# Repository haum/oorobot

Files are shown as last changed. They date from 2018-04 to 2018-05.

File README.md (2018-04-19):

logo_s

# OoRoBoT : Un robot éducatif à construire soi-même

L'idée est de créer un robot éducatif destiné aux enfants de maternelle et élémentaire sur le principe de [la BeeBot](http://www.robotsenclasse.ch/robots-en-classe/beebot), tout en suivant les contraintes suivantes :
- Mettre le projet en OpenSource : page github avec le code, la liste de matériel et les plans nécessaires
- Utiliser du matériel électronique standard (Arduino) et peu onéreux
- Éviter les opérations "complexes" (soudure, usinage)

Au fil des évolutions du projet, l'OoRoBoT apporte tout un lot de fonctionnalités complémentaires :
- Présence d'un écran LCD de 2 lignes de 16 caractères permettant à l'enfant de visualiser le programme qu'il écrit. Cet écran associé au clavier permet aussi de régler le robot très précisement
- Ajout d'une interface Bluetooth permettant de piloter le robot à distance et ainsi permettre de lui donner des ordres complexes (boucles, tracé d'arc de cercle ...)
- Ajout d'un servomoteur afin de baisser/lever un crayon

Actuellement le robot peut être utilisé de deux façons différentes (comme indiqué dans sur [ce poster](doc/com/oorobot_poster-LIGHT.pdf)) :
- Pour les enfants de 4 à 7 ans : programmer des parcours sur des plateaux (voir les plateaux disponibles dans le [répertoire /doc/exercices](/doc/exercices))
- Pour les enfants de 7 à 12 ans : réaliser des tracés avec un langage de programmation par blocs. Vous pouvez vous entrainer à faire des tracés sur [cette page Web](https://orange-opensource.github.io/oorobot/blocks/index.html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) (reproduction de l'interface disponible dans l'application Android)

Pour suivre l'évolution du robot vous pouvez suivre le mot dièse [#OoRoBoT sur Twitter](https://twitter.com/hashtag/OoRoBoT?src=hash)

## Genèse du projet 

J'ai eu cette idée en discutant avec une professeure des écoles (Maître Formatrice) qui utilisait des BeeBot dans son école. Actuellement on trouve de nombreux de robots sur le marché mais ils sont souvent trop "compliqués" pour faire des activités simples. Dans l'exemple que j'ai observé, les BeeBot étaient utilisées pour apprendre le déplacement relatif et la suite de commandes à des enfants de grande section. J'ai cherché un équivalent moins cher et/ou OpenSource je n'ai rien trouver de probant.

Je me suis donc lancé dans ce projet profitant des imprimantes 3D disponibles au travail, de mes compétences en Arduino et du temps donné par mon employeur pour réaliser des *side-project*. L'idée était aussi de pouvoir utiliser ce robot comme traceur (comme [la mythique tortue "Jeulin" des années 80](http://www.tortue-jeulin.com/articles.php?lng=fr&pg=3&mnuid=2&tconfig=0)).
 
Au final, le robot revient à moins de 30€ (si vous le fabriquer vous-même) et ne demande aucune soudure. Le châssis peut être imprimé sur une imprimante 3D possédant un plateau de 20cm sur 20cm ou en utilisant une découpeuse laser.

Le nom du projet **OoRoBoT** pour **Orange Open ROBOT**.

oorobot_cote_s

## Le principe

- On allume le robot
- L'enfant peut lui donner les ordres suivants :
    - avancer
    - reculer
    - tourner à droite à angle droit
    - tourner à gauche à angle droit
    - faire une pause
    - effacer la dernière commande
    - *lever ou baisser le crayon* au centre du robot
- À chaque appui sur un bouton d'ordre ce dernier s'affiche sur l'écran LCD. NB : L'écran LCD ne peut afficher que 32 ordres (l'Arduino quant à lui peut en gérer plus)
- En cas d'erreur l'enfant peut effacer le dernier ordre ou tout son programme par un appui long sur le bouton "effacer"
- Quand l'enfant le veut il peut lancer son programme avec le bouton "Lancer"
- Le robot éxecute alors chaque ordre en faisant une courte pause entre chacun d'entre eux.
- Quand le programme est terminé, la liste des ordres se réaffiche et l'enfant peut faire d'éventuels ajustements.
- On peut accéder au réglage des paramètres en faisant un appui long sur un bouton dédié. Les paramètres sont :
    - La distance parcourue pour les déplacements "avancer" et "reculer".
    - Le nombre de pas que les moteurs doivent faire pour effectuer un tour complet (qui peut varier selon la surface sur laquelle doit évoluer le robot)
    - Le nombre de pas que les moteurs doivent faire pour avancer de 10cm

Pour changer de ligne il faut appuyer sur les touches "avancer" ou "reculer", pour changer les valeurs il faut appuyer sur les touches "tourner à droite" et "tourner à gauche". Un appui long sur ces touches permet d'augmenter la valeur d'incrément.

Pour annuler les changements des paramètres il faut appuyer sur le bouton "effacer". Pour quitter les paramètres en les sauvegardant il faut apppuyer sur la touche "lancer" ou "paramètre"

Le robot peut aussi être programmé à distance (Bluetooth) via une application Android (disponible [ici](apk/oorobot.apk)).

## Le matériel

composant_s

### À acheter :
- 1 [arduino nano](https://fr.aliexpress.com/store/product/Nano-CH340-ATmega328P-MicroUSB-Compatible-for-Arduino-Nano-V3/1950989_32572612009.html) : 2.40€ (3.50€ [avec le cable USB](https://fr.aliexpress.com/item/Nano-V3-ATmega328P-CH340G-USB-2-0-data-CABLE-50cm-Compatible-for-Arduino-Nano-V3-0/32759066704.html)) 
- 1 [sensor shield](https://fr.aliexpress.com/store/product/A47-1-pcs-SAMIORE-ROBOT-UNO-Bouclier-Nano-Bouclier-pour-NANO-3-0-et-UNO-R3/1022067_32832972324.html) : 1€
- 2 [moteurs pas à pas](https://fr.aliexpress.com/item/5V-Stepper-Motor-28BYJ-48-With-Drive-Test-Module-Board-ULN2003-5-Line-4-Phase/32608569300.html) : 4.50€
- 1 [clavier 3x4 boutons](https://fr.aliexpress.com/item/Button-Keypad-3x4-module/32530917534.html) : 2,00€
- 1 [écran LCD 2x16 caractères sur interface I2C](https://fr.aliexpress.com/store/product/LCD1602-I2C-LCD-1602-module-Blue-screen-IIC-I2C-for-arduino-LCD1602-Adapter-plate/1022067_32651314933.html) : 1,70€
- 1 [conteneur de piles LR6](https://fr.aliexpress.com/item/New-6-x-AA-Battery-Case-Storage-Holder-With-DC2-1-Power-Jack-For-Arduino/32801965248.html) : 1,10€
- 1 [servo-moteur](https://fr.aliexpress.com/item/2016-NEW-SG90-Servo-mini-micro-9g-for-Rc-helicopter-Airplane-Foamy-Plane-Car-Boat/32717599656.html) pour lever/baisser un crayon: 1.20€
- 2 [roues "billes"](https://fr.aliexpress.com/item/CY-12A-12mm-bearing-smart-car-casters-small-maverick-eye-round-steel-ball-omni-wheel-universal/32705899129.html) : 2,50€
- 1 [lot de cables "dupont" de 20cm](https://fr.aliexpress.com/item/Free-Shipping-80pcs-dupont-cable-jumper-wire-dupont-line-female-to-female-dupont-line-20cm-1P/1699285992.html) : 0,85€
- [des vis M2x5mm ](https://fr.aliexpress.com/item/50Pcs-lot-Screw-M2-5-of-Screws-Nuts-Assortment-Bolts-Screw-Spike-Round-Head-Screw-2mm/32722845879.html) : 0,70€
- [des vis M3x5mm ](https://fr.aliexpress.com/item/M3-x-5mm-Cross-Flat-Head-Countersunk-Bolts-Machine-Screws-100Pcs/32762532904.html) : 1€ : il y en a besoin de 8 en tout par robot, vous pouvez récupérer des vis utilisées pour tenir les disques durs ou les cartes mères

Pour le Bluetooth :
- 1 [module Bluetooth HC-06](https://fr.aliexpress.com/store/product/HC-06-Bluetooth-serial-pass-through-module-wireless-serial-communication-from-machine-Wireless-HC06-for-arduino/1022067_32284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) : 2.60€
- 1 [bouton on/off](https://fr.aliexpress.com/item/1pcs-Power-on-off-switch-JST-Connector-Receiver-Switch-For-RC-Boat-Car-Flight-two-way/32636753090.html) (choisir le moins cher): 1€
- ~~1 [convertisseur de niveau](https://fr.aliexpress.com/item/Logic-Level-Converter-Bi-Directional-3-3V-5V-4-Chanels/32713434790.html) : 0.50€~~ : ce composant est **optionel**, en effet bien que la documentation du module Bluetooth HC-06 indique que le niveau de tension pour la communication doit être à 3.3V, le module fonctionne bien avec la tension native de l'Arduino (5V)

Soit un total d'environ **21€** (ou **25€** avec le Bluetooth) et surtout **aucune soudure n'est nécessaire** ! De plus les moteurs pas-à-pas, bien que lents, sont très silencieux.

### À récupérer :
- 2 grands élastiques pour les pneus.
- des petits élastiques pour le système permettant de baisser/lever un crayon
- Un tube de colle liquide (forte, à bois ...) qui est utile pour coller certaines parties ou au cas où les trous de vis soient un peu trop grands. C'est aussi pratique pour coller les elastiques sur les roues ou pour éviter que la prise du conteneur de piles ne se dévisse.

### Notes sur l'alimentation électrique
- Dans la liste de matériel j'ai indiqué de prendre un conteneur de 6 piles LR6 (soit 9V). Ces piles sont à brancher sur l'entrée régulée du shield. Cette solution permet d'assurer la stabilité de l'alimentation du robot même quand les piles commencent à faiblir. L'inconvénient c'est que ça oblige à avoir 6 piles pour chaque robot.
- On peut utiliser un contenur de 4 piles, mais ce dernier doit être branché directement sur l'alimentation 5V derrière le régulateur (celui-ci est prévu pour des tensions de 7V à 12v). Le problème de cette solution est qu'elle surcharge un peu les composants au début de vie des piles et peut entrainer des instabilités de fonctionnement en fin de vie des piles.
- On peut utiliser une batterie 5V pour téléphone portable de [ce style](https://fr.aliexpress.com/item/Remax-2500mAh-Pino-Small-Mobile-Phone-Large-Capacity-Mini-Power-Bank-General-Charge-Treasure-Extra-Power/32790051749.html) à 7€ à brancher directement sur la prise micro-USB de l'Arduino. 

Les batteries ont l'avantage d'être bien régulées (et peuvent donc être directement branchées sur l'Arduino). L'autre avantage est qu'elles disposent, la plupart du temps, d'un bouton marche/arrêt.

Sans optimisation, lors des premiers essais réalisés on mesure que lors des déplacements le montage consomme 0,36A, puis quand l'afficheur LCD est allumé il consomme 0,05A et quand il ne fait rien 0,03A.

## Le châssis

- Il doit être solide
- Les roues doivent être assez grandes pour que le robot avance assez rapidement
- Il faut garder un trou dans l'axe des roues pour pouvoir insérer un crayon

Les parties conçues (voir répertoire 3D) :
- Deux roues rapides à imprimer de diamètre 9cm avec les encoches pour insérer en force les moteurs pas-à-pas et des rebords pour retenir les élastiques
- Un châssis contenant les supports nécessaires pour fixer les composants. Utilisation des contrôleurs des moteurs pas-à-pas pour faire des "yeux".
 
L'impression de la version actuelle des pièces a pris 5h20 et consommé 98g de matière (PLA) avec les réglages suivant (sur une imprimante Volumic Stream20Pro):
- qualité normale (200 microns)
- densité de remplissage : 20%
- épaisseur des bords : 0.8 mm (au lieu de 1.2mm par défaut sur les profils Cura de l'imprimante)
 
A la vue des demandes qui commencent à affluer pour avoir un robot, j'ai conçu un modèle à fabriquer avec une découpeuse laser comme celle disponible au [FabLab de Lannion](http://www.fablab-lannion.org/). Cette version en découpe laser permet maintenant de lever/baisser un crayon. 

## Historique

### La version en MDF

Ajout d'un système pour pouvoir lever et baisser un crayon.

oorobot mdf

### Le char

Déplacement des roues au centre du châssis. Centre de gravité descendu au maximum.

oorobot char

### Le chariot

Premier "vrai" modèle. Présence d'une roue encodeuse pour le réglage du pas qui a été enlevé dans la version actuelle (utilisation du clavier)

oorobot chariot

### Le prototype

proto

## Le code
 
Vous trouverez 2 programmes dans le répertoire Arduino de ce dépôt :
- init-bluetooth: ce programme permet d'initialiser le module Bluetooth (lui donner un nom au format "OoRoBoT-XXXX" et affecter le code d'appairage 0000). Ce programme n'est à charger qu'une seule fois.
- oorobot: le programme principal du robot

## Le montage des composants

Brancher l'Arduino Nano sur le "sensor shield".

Branchement du clavier sur le port A0 (détacher un groupe de 3 fils):
- Brancher un fil entre la broche **VCC** du clavier et la broche **V** de l'Arduino
- Brancher un fil entre la broche **GND** du clavier et la broche **G** de l'Arduino
- Brancher un fil entre la broche **Out** du clavier et la broche **S** de l'Arduino

Branchement de l'écran LCD sur une des ligne I2C (détacher un groupe de 4 fils): 
- Brancher un fil entre la broche **GND** de l'écran et la broche **GND** la ligne I2C choisie
- Brancher un fil entre la broche **VCC** de l'écran et la broche **5V** la ligne I2C choisie
- Brancher un fil entre la broche **SDA** de l'écran et la broche **SDA** la ligne I2C choisie
- Brancher un fil entre la broche **SCL** de l'écran et la broche **SCL* la ligne I2C choisie

Branchement des cartes de contrôle des moteurs pas-à-pas :
- Moteur roue droite sur les ports 4, 5, 6 et 7 de l'Arduino (détacher un groupe de 4 fils pour les broches **IN** et un groupe de 2 fils pour les broches **-** et **+**):
    - Brancher un fil entre la broche **IN1** du contrôleur et la broche **S** du port 4 de l'Arduino
    - Brancher un fil entre la broche **IN2** du contrôleur et la broche **S** du port 5 de l'Arduino
    - Brancher un fil entre la broche **IN3** du contrôleur et la broche **S** du port 6 de l'Arduino
    - Brancher un fil entre la broche **IN4** du contrôleur et la broche **S** du port 7 de l'Arduino
    - Brancher un fil entre la broche **-** du contrôleur et la broche **G** du port 7 de l'Arduino
    - Brancher un fil entre la broche **+** du contrôleur et la broche **V** du port 7 de l'Arduino
- Moteur roue gauche sur les ports 8, 9, 10 et 11 de l'Arduino (détacher un groupe de 4 fils pour les broches **IN** et un groupe de 2 fils pour les broches **-** et **+**):
    - Brancher un fil entre la broche **IN1** du contrôleur et la broche **S** du port 8 de l'Arduino
    - Brancher un fil entre la broche **IN2** du contrôleur et la broche **S** du port 9 de l'Arduino
    - Brancher un fil entre la broche **IN3** du contrôleur et la broche **S** du port 10 de l'Arduino
    - Brancher un fil entre la broche **IN4** du contrôleur et la broche **S** du port 11 de l'Arduino
    - Brancher un fil entre la broche **-** du contrôleur et la broche **G** du port 10 de l'Arduino
    - Brancher un fil entre la broche **+** du contrôleur et la broche **V** du port 11 de l'Arduino

Brancher les moteurs pas-à-pas sur les contrôleurs. Marquer les moteurs droite et gauche afin de les différencier facilement lors du montage final.

Branchement du servo-moteur sur le port 3 : brancher le câble de que le fil marron soit sur la broche **G** du port 3, le fil rouge sur la broche **V** et le fil orange sur la broche **S**

**Attention** pour les personnes ayant commandé [ce modèle de *shield*](https://fr.aliexpress.com/store/product/Nano-I-O-expansion-Shield-for-Arduino-Nano-V3-pinout-Assembled/1950989_32633286806.html) il faut inverser les fils rouge et marron du servomoteur! Pour cela utiliser un petit tournevis plat et soulever légèrement le petit ergot au bout d'un des fils (rouge ou marron) puis tirer légèrement sur ce dernier, il devrait venir facilement. Faire de même avec le deuxième fil. Rebrancher les fils en les inversant par rapport à leur position initiale. Vous pourrez maintenant faire en sorte de respecter la consigne pour que "le fil marron soit sur la broche **G** du port 3, le fil rouge sur la broche **V** et le fil orange sur la broche **S**" 

Branchement du module Bluetooth :
- Brancher le cable de l'interrupteur (détacher un groupe de 2 fils):
    - Brancher un fil entre la broche **G** du port 12 de l'Arduino en face du fil noir de l'interrupteur
    - Brancher un fil entre la broche **V** du port 12 de l'Arduino en face du fil rouge de l'interrupteur
    - Brancher l'autre extrémité de l'interrupteur de manière à ce que le fil noir soit en face de la broche **GND** du module Bluetooth et le fil rouge en face de la broche **+5V**
- Brancher le module à l'Arduino (détacher un groupe de 2 fils) :
    - Brancher un fil entre la broche **RX** du module Bluetooth et la broche **S** du port 13 de l'Arduino
    - Brancher un fil entre la broche **TX** du module Bluetooth et la broche **S** du port 12 de l'Arduino

Découper les modèles de touches ([disponibles ici](doc/menu/menu.pdf)) et les insérer dans le clavier, pour cela il faut sortir les touches (ça vient facilement en tirant dessus) puis enlever la partie transparente (vous pouvez utiliser une paire de ciseaux pour faire levier), placer les découpes et remettre en place les touches.

Télécharger et installer le programme [Arduino IDE ](https://www.arduino.cc/en/Main/Software) sur votre PC. Brancher l'Arduino avec un cable USB sur votre PC. Vous devriez voir apparaître dans le menu "Outils/Port" une nouvelle entrée (*/dev/ttyUSBx* sous Linux, *COMx* sous Windows). Sélectionner dans "Outils/Type de carte" le modèle "Arduino Nano"

Télécharger le programme [init-bluetooth](arduino/init-bluetooth) et l'ouvrir avec *Arduino IDE*. Téléverser le programme (2ème bouton en haut à gauche de l'interface) sur l'Arduino. Ce programme va configurer le module Bluetooth pour :
- Donner un nom au format "OoRoBoT-XXXX"
- Configurer le code PIN à 0000
- Configurer la vitesse de communication à 9600 bauds

Attendre quelques secondes puis vérifier que le robot est bien visible en Bluetooth. Vous pouvez utiliser le "moniteur série" (Menu "Options/Moniteur série") du programme Arduino IDE pour voir où en est la configuration du Bluetooth.

Télécharger le programme [oorobot](arduino/oorobot) et l'ouvrir avec le programme *Arduino IDE*. Il faut installer les dépendances suivantes en allant dans le menu "Croquis/Inclure une bibliothèque/Gérer les bibliothèques" puis en cherchant les bibliothèques à installer :
- **AccelStepper** v1.57.1 by Mike McCauley
- **LiquidCrystal I2C** v1.1.2 by Frank de Brabander

Téléverser ensuite le programme *oorobot* sur l'Arduino. Ce programme va piloter tout le robot. Après le téléchargement il est temps de vérifier que le câblage est bien réalisé :
- Vérifier le branchement du clavier, un appui sur un bouton doit afficher des caractères sur l'écran LCD
- Vérifier le contraste de l'écran : ce dernier doit s'allumer au démarrage, par contre si vous ne voyez rien, pas de panique c'est peut-être tout simplement parce que le contraste est mal réglé. Pour changer ce paramètre il suffit de tourner le petit potentiomètre derrière l'écran avec un tournevis cruciforme jusqu'à avoir un bon contraste entre l'affichage des caractères et le fond de l'écran
- Marquer le dessus du servo-moteur : l'axe du moteur doit être sur la gauche du composant quand la partie mobile est devant vous. Vérifier que ce dernier bouge bien si vous appuyer sur les boutons lever/baisser le crayon
- Vérifier que les moteurs fonctionnent bien : lancer une commande "avance" pour vérifier que les moteurs tournent dans le bon sens, faire de même avec une commande "tourne à droite".
- Vérifier le sens de l'interrupteur : jouer avec le bouton de l'interrupteur pour voir dans quelle position il allume ou éteint le module Bluetooth. Veillez à noter ces états afin de bien positionner plus tard l'interrupteur sur le châssis.
- Vérifier que le module Bluetooth fonctionne : activer le Bluetooth sur votre téléphone/tablette et vérifier que vous pouvez bien vous appairez avec le robot (code PIN 0000). Si vous le pouvez vérifier ensuite que vous pouvez piloter le robot avec l'application Android fournie (voir plus bas)

Tout est OK? Vous pouvez passer au montage des composants sur le châssis.

[Ordre de montage des composants sur le châssis 2D](2d/)

Ordre de montage des composants sur le châssis 3D :

montage2

- Débrancher les moteurs pas-à-pas des contrôleurs
- Fixer les roues en force sur les moteurs pas-à-pas
- Faire passer les contrôleurs des moteurs dans les trous placés derrière le support de l'Arduino
- Visser l'Arduino sur son support
- Visser les controleurs sur leurs support (garder la cohérence contrôleur moteur droit fixer à droite du robot)
- Visser le clavier sur son support en passant les cables entre le châssis et le clavier
- Plier les broches de l'écrans pour les mettre à la verticale. Visser ensuite l'écran sur le châssis
- Entrer en force les moteurs pas-à-pas dans leur emplacement. Faire passer leurs fils jusqu'à leur contrôleur respectif. Visser ensuite les vis M3 pour maintenir les moteurs au châssis
- Placer le bloc de pile devant l'Arduino

## Pilotage avec le Bluetooth
 
Le robot est maintenant pilotable via une application pour mobile/tablette (Android pour le moment) conçue par un collègue (merci Julien) avec Ionic (voir répertoire OoRobotIonicApp) et utilisant Blockly :

app

Vous pouvez télécharger l'APK [ici](apk/oorobot.apk) 

Afin d'envoyer les programmes sur l'Arduino on a définit un pseudo langage simple sous la forme :
```
[<lettre>;<chiffre>*]*
```

Combinaisons possibles
- U (up). Les chiffres correspondent aux nombres de mm à faire.
- D (down). Les chiffres correspondent aux nombres de mm à faire.
- R (right). Les chiffres correspondent à l'angle à faire.
- L (left). Les chiffres correspondent à l'angle à faire.
- B (begin loop). Les chiffres correspondent au nombre de répétitions des commandes suivantes (jusqu'à trouver la lettre E)
- E (end loop). Pas de chiffre attendu
- P (pause). Faire une attente de x ms
- W (waiting). Les chiffres correspondent au temps d'attente (en ms) entre 2 mouvements.
- ! baisser le crayon
- | lever le crayon
- c pour préparer un arc de cercle, les chiffres correspondent au diamètre de l'arc
- a lance le début du traçage de l'arc en prenant comme angle les chiffres qui suivent

Pour dessiner un héxagone :
```
!U50R60U50R60U50R60U50R60U50R60U50R60|
```
ou
```
!B6U50R60E|
```
## Licences

Le code est sous [GPL2](https://www.gnu.org/licenses/old-licenses/gpl-2.0.fr.html), les modèles 3D et la documentation sont sous [CC-BY-SA](https://creativecommons.org/licenses/by-sa/2.0/deed.fr).

## Les projets équivalents

- [escornabot](http://escornabot.com/web/en) : un projet espagnol vraiment dans le même esprit mais qui demande un peu connaissance technique pour la partie clavier (soudure)

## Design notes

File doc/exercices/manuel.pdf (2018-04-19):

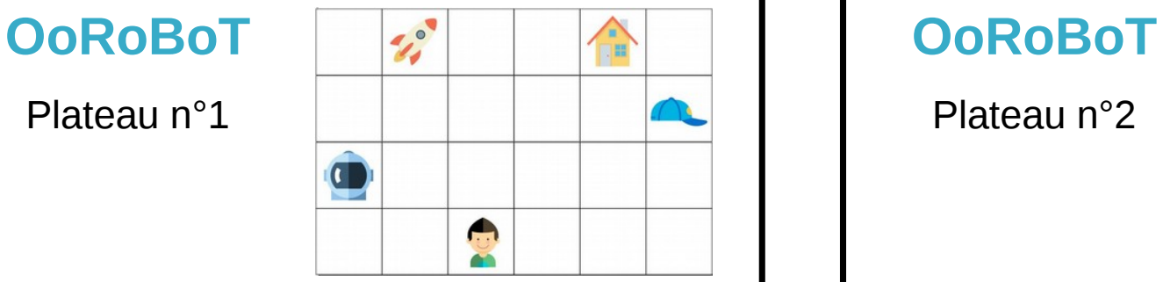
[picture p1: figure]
OoRoBoT

### Plateau n°1

Le plateau va permettre de découvrir le fonctionnement du OoRoBoT en faisant quelques exemples.

Voici les questions que vous pouvez poser :

1 – Quel chemin peut prendre l'enfant pour aller jusqu'à à la maison ?
2 – Même chose avec la fusée
3 – Maintenant l'enfant doit prendre un objet sur son chemin (La casquette pour aller à la maison, le casque de cosmonaute pour rejoindre la fusée)

Une fois le chemin en tête l’enfant peut taper les commandes sur l’OoRoBoT grâce aux touches directionnelles.

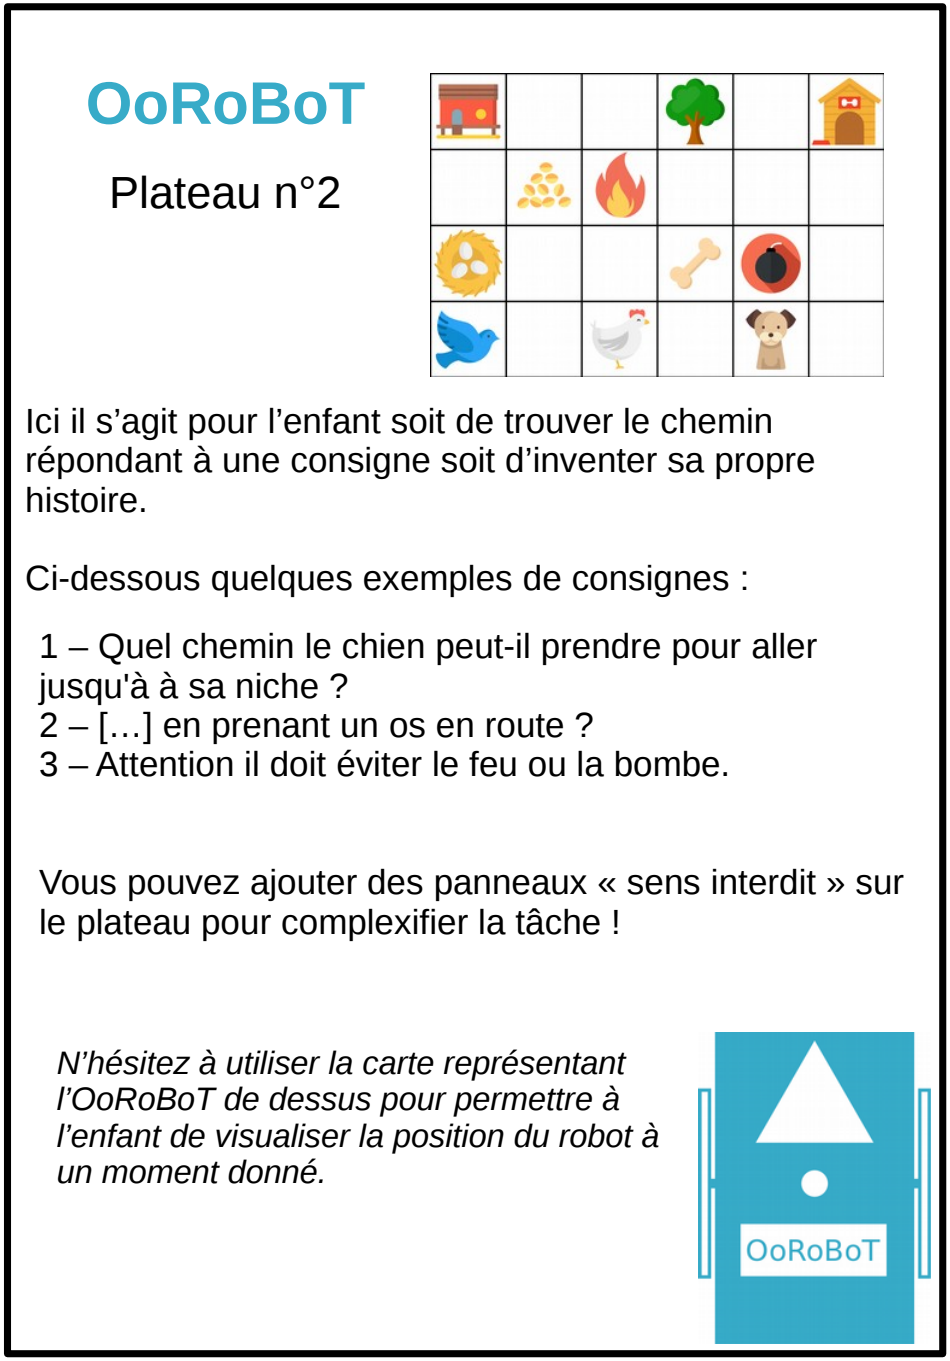
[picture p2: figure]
Plateau n°2; histoire.; jusqu'à à sa niche ? 2 – […] en prenant un os en route ?; le plateau pour complexifier la tâche !; l’OoRoBoT de dessus pour permettre à; un moment donné.

Ici il s’agit pour l’enfant soit de trouver le chemin répondant à une consigne soit d’inventer sa propre

Ci-dessous quelques exemples de consignes :

1 – Quel chemin le chien peut-il prendre pour aller

3 – Attention il doit éviter le feu ou la bombe.

Vous pouvez ajouter des panneaux « sens interdit » sur

Il n'y a pas de bonne réponse, tous les chemins sont acceptés dès lors que le point de départ et d'arrivée sont respectés.
Des cartes « flèches » sont à disposition de l’enfant pour qu’il puisse s'il le souhaite écrire son programme avant de le taper sur l’OoRoBoT.

N’hésitez à utiliser la carte représentant

l’enfant de visualiser la position du robot à

# OoRoBoT

### Plateau n°3

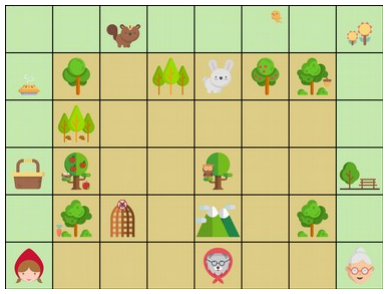
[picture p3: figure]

Ce plateau de 48 cases va permettre l’écriture de programmes plus longs et complexes que les précédents

Comme pour le niveau 2 il s’agit ici pour l’enfant de répondre à une consigne ou d’inventer sa propre histoire.

Les personnages, le chemin (vert), la forêt l’aideront à créer son scénario.

- Comment le petit chaperon rouge peut-il rejoindre sa grand-mère ?
- Que peut-il faire si le loup est sur son chemin (Passer prendre la cage à loup ou le contourner) ?
- Qu’est ce que le petit chaperon rouge peut apporter à sa grand-mère (galette, champignons, pommes, œufs, fleurs…) ?
- Les animaux aussi peuvent aussi avoir leurs histoires ; elles sont à inventer !

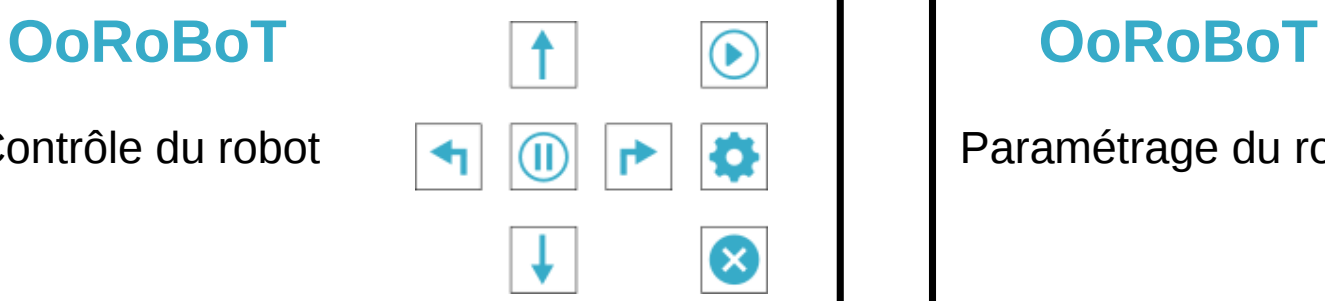
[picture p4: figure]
OoRoBoT

### Contrôle du robot

Le robot se programme à l’aide du clavier :

Le robot avancera d’une case

Le robot reculera d’une case

Le robot tournera à gauche

Le robot tournera à droite

Efface la dernière commande
Un appui long efface toutes les commandes

Lance le programme

Quand le robot exécute le programme on peut l’arrêter en appuyant sur n’importe quelle touche du clavier

Le robot avancera d’une case

Le robot reculera d’une case

Le robot tournera à gauche

Le robot tournera à droite

Le robot fera une pause

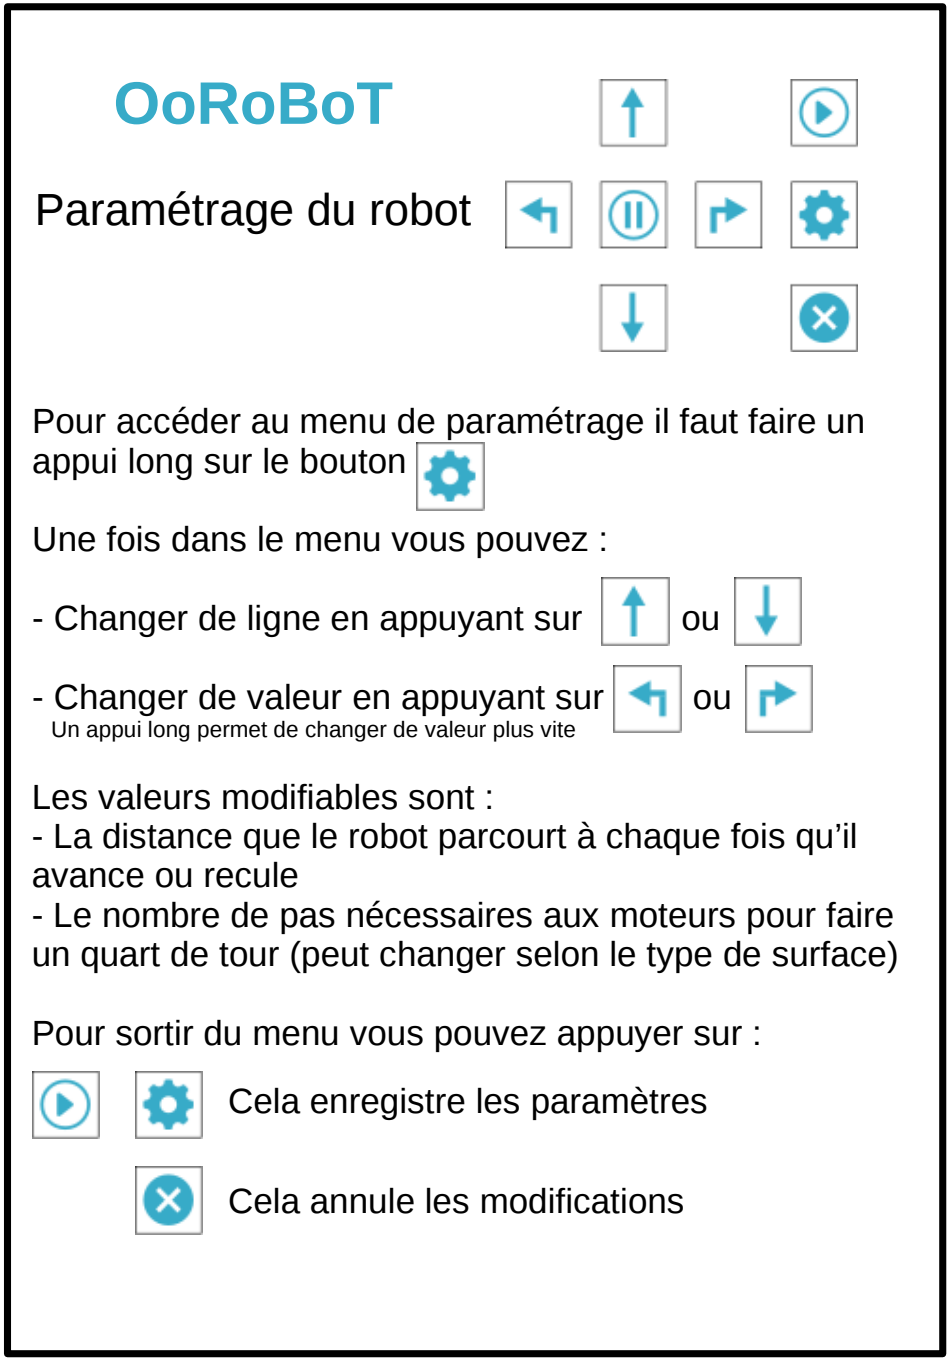
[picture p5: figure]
Paramétrage du robot; appui long sur le bouton; Une fois dans le menu vous pouvez :; - Changer de ligne en appuyant sur; - Changer de valeur en appuyant sur; Les valeurs modifiables sont :; avance ou recule; Cela enregistre les paramètres; Cela annule les modifications

Pour accéder au menu de paramétrage il faut faire un

Un appui long permet de changer de valeur plus vite

- La distance que le robot parcourt à chaque fois qu’il
- Le nombre de pas nécessaires aux moteurs pour faire un quart de tour (peut changer selon le type de surface)

Pour sortir du menu vous pouvez appuyer sur :

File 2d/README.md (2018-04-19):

# OoRoBoT: Notice de montage de la version en MDF

## Matériel nécessaire
- Un tournevis cruciforme fin (aimanté si possible)
- Un tube de colle liquide (type colle forte pour les plus pressés)
- Du temps : comptez une heure pour le montage complet

## Conseils 
- Ne vissez pas les vis "à fond" pour fixer les composants dès le début. Placez votre première vis, faites quelques tours de tournevis pour que la vis ne sorte plus puis passer à la vis suivante. Quand toutes les vis sont en place pour tenir votre composant vous pouvez les serrez complétement sur le support.
- Vérifier bien que tous les composants fonctionnent avant de faire ce montage.

## Le montage 

- Montez le support externe du crayon :
    
support_crayon_exterieur

- Montez le support interne du crayon (ici version <= 13) :

support_crayon_interieur    
    
- Collez le support Arduino sur la partie dépassant du support interne du crayon (ici version > 13) :
    
coller_support_arduino_support_crayon    
    
- Placez l'interrupteur (en ayant auparavant dévissé le « cache » fourni) en réutilisant les vis (attention à bien retenir leur sens pour respecter les positions arrêt/marche) :
    
bas_on-off_bluetooth
     
- Fixez le servomoteur sur son support (utilisez les vis fournies avec le servomoteur), bien faire attention au sens de rotation, l'axe doit être sur la droite comme sur la photo ci-dessous :

 support_servomoteur
    
- Placez le support du servomoteur sur la plaque de fond :

bas_servomoteur_on-off

- Rabaissez (ou coupez) les broches qui sont au-dessus de l’arduino pour faciliter le montage des côtés : 
    
baisser_broches_arduino

- Vissez l’arduino sur le support Arduino qui est lui-même collé sur le support interne du crayon (ici version <= 13):
 bas_support_crayon    
    
- Fixez le clavier :
    
support_clavier

- Fixez l’écran (vous pouvez plier doucement les broches de l'écran pour faciliter le montage de la partie haute):
    
haut_ecran

- Fixez les contrôleurs des moteurs pas-à-pas (et passez le séparateur derrière les contrôleurs) :
    
support_controleurs_moteurs

passage_sepatation
  
- Fixez les moteurs sur les plaques des côtés (vis M3) et placez les rondelles autour des moyeux :

cote_rondelle_avant_roue

- Collez des élastiques autour des roues
- Encastrez les roues (en tenant bien l’arrière des moteurs pour que les vis ne sortent pas) et ajoutez une des formes de "bloqueur" (petit ou grand selon ce que vous préférez) :
    
cote_roue_bloqueur
    
- Encastrez le support des contrôleurs des moteurs pas-à-pas, le séparateur et le support du clavier entre les deux côtés du châssis (utilisez de la colle pour maintenir les côtés au besoin). **Attention** : comme montré ci-dessous il faut que les fils de l'écran sortent par le haut du montage :

bas_cote_avant_montage

- Encastrez les côtés sur le fond du châssis

bas_cote_apres_montage

- **Attention** : avant de continuer le montage, je vous conseil de vérifier que tous les composants fonctionnent toujours bien ! Il se peut que des fils sortent des broches durant les manipulations précecédentes.

- Glissez le fond du boitier à piles entre le support des contrôleurs de moteurs pas-à-pas avec la séparation :

passage_fond_boitier_piles 

- Entrez cette pièce dans l'encoche visible sous les contrôleurs de moteur pas-à-pas :

mettre_fond_boitier_dans_encoche

- Poussez (par le haut du robot) sur cette pièce, elle devrait s'encastrer pour se positionner parallèlement au bas du robot (faire en sorte que des fils ne gênent pas cette manipulation)

- Encastrez la partie supérieure et à partir des version>=12, encastrez les barres de maintien sur les côtés. Collez le cache autour de l’écran (Attention sur la photo le montage est fini, à cette étape le support à crayon et le boitier de piles ne doivent pas être mis en place) : 

 finition
 
- Retournez le robot et fixez les roues à bille (vis M3) :

fixer_roues_bille
 
- Pour les version >13 collez le petit rectangle sur l'ovale gravé pour fabriquer un petit cache pour le connecteur Arduino :
preparer_colle_cache_prise_arduino cache_prise_arduino

Et pour terminer :
- Si ce n'est pas déjà fait, découpez les modèles de touches ([disponible ici](../doc/menu/menu.pdf)) et insérez-les dans le clavier, pour cela sortez les touches (ça vient facilement en tirant dessus) puis enlevez la partie transparente (vous pouvez utiliser une paire de ciseaux pour faire levier), placez les découpes et remettez en place les touches.
- Insérer le support de crayon externe dans le robot, vous pouvez mettre un élastique entre le dessus du robot et ce support pour avoir une meilleure pression sur le crayon
- Calibrer votre robot via le menu "paramètres" (appui long sur le bouton au milieu de la colonne  la plus à droite du clavier):
    - Le nombre de pas que les moteurs doivent faire pour effectuer un 1/4 de tour : pour cela, avec le clavier entrez le programme "tourner à droite" 4 fois et lancez le. Si le robot n'a pas fait exactement un tour, rentrez dans le menu "paramètres" et changez le nombre de pas, appuyez sur le bouton start, vous reviendrez sur votre programme que vous pourrez relancer pour affiner votre réglage
    - Le nombre de pas que les moteurs doivent faire pour avancer de 10 cm, procédez comme pour le réglage d'un tour complet. Vous pouvez utiliser la fonction de dessin avec un crayon pour mesurer la précision du robot.

## Fichiers

Pour ceux qui veulent modifier ou fabriquer la structure :
- oorobot.svg : le modèle réalisé avec Inkscape
- oorobot.dxf : export DXF pour les découpeuses laser

Correspondance des couleurs :
- Vert : couche de travail, ne pas prendre en compte pour la découpe ou la gravure
- Rouge : couche à découper
- Noire : couche à graver

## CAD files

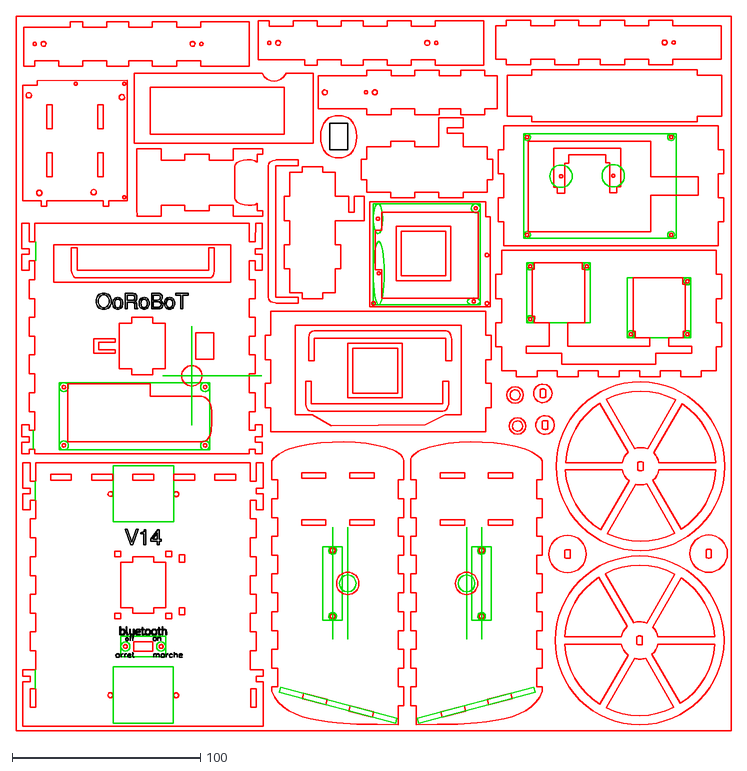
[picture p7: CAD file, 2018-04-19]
2d/oorobot.dxf
379.9 x 379.9

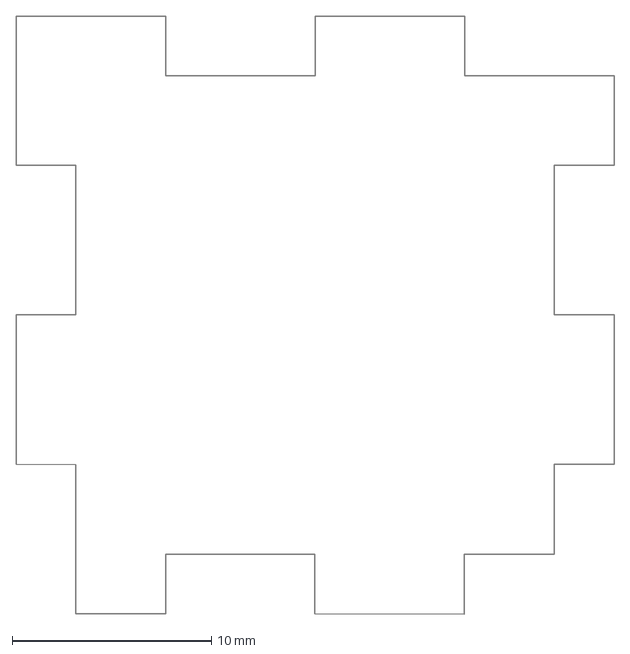
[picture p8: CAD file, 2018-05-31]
des/theKube.dxf
30.0 x 30.0 mm

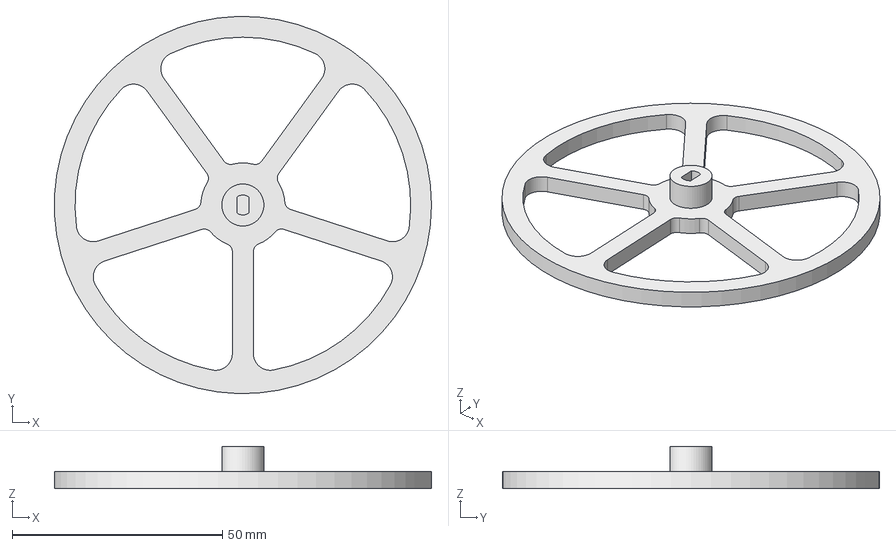
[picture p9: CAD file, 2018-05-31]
Roues3d/roues.fcstd
89.6 x 89.7 x 10.0 mm

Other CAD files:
Roues3d/roue.stl

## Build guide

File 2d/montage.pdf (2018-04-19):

# OoRoBoT : Notice de montage

## Matériel nécessaire

- Un tournevis cruciforme fin (aimanté si possible)
- Un tube de colle liquide (type colle forte pour les plus pressés)
- 2 grands élastiques pour les roues et un petit pour le support de crayon

## Montage de la partie électronique

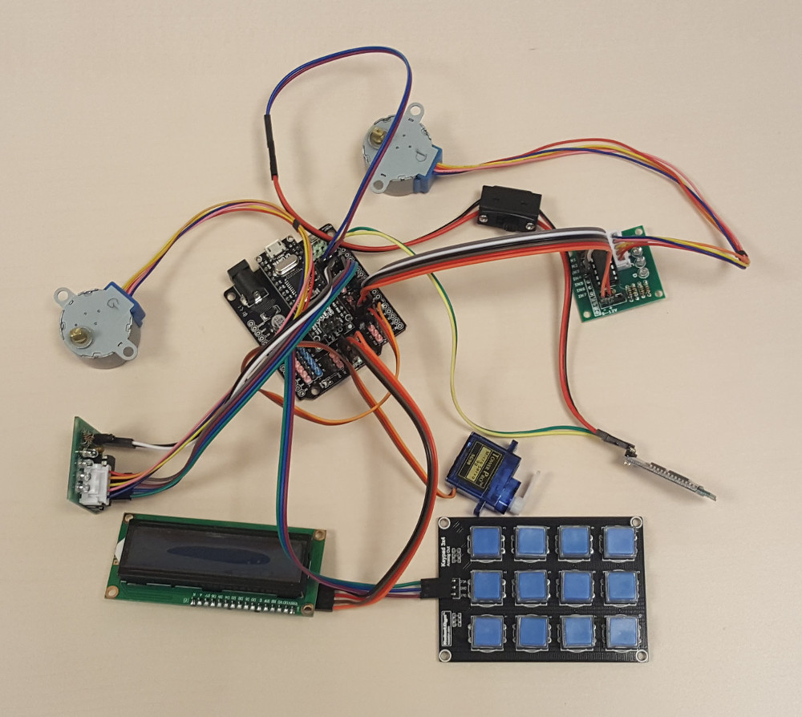
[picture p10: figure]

Brancher l'Arduino Nano sur le "sensor shield".
Branchement du clavier sur le port A0 (détacher un groupe de 3 fils):
- Brancher un fil entre la broche VCC du clavier et la broche V de l'Arduino
- Brancher un fil entre la broche GND du clavier et la broche G de l'Arduino

Page 1 sur 13

- Brancher un fil entre la broche Out du clavier et la broche S de l'Arduino

Branchement de l'écran LCD sur une des ligne I2C (détacher un groupe de 4 fils):
- Brancher un fil entre la broche GND de l'écran et la broche GND la ligne I2C choisie
- Brancher un fil entre la broche VCC de l'écran et la broche 5V la ligne I2C choisie
- Brancher un fil entre la broche SDA de l'écran et la broche SDA la ligne I2C choisie
- Brancher un fil entre la broche SCL de l'écran et la broche *SCL la ligne I2C choisie

Branchement des cartes de contrôle des moteurs pas-à-pas :
- Moteur roue droite sur les ports 4, 5, 6 et 7 de l'Arduino (détacher un groupe de 4 fils pour les broches IN et un groupe de 2 fils pour les broches - et +):
- Brancher un fil entre la broche IN1 du contrôleur et la broche S du port 4 de l'Arduino
- Brancher un fil entre la broche IN2 du contrôleur et la broche S du port 5 de l'Arduino
- Brancher un fil entre la broche IN3 du contrôleur et la broche S du port 6 de l'Arduino
- Brancher un fil entre la broche IN4 du contrôleur et la broche S du port 7 de l'Arduino
- Brancher un fil entre la broche - du contrôleur et la broche G du port 7 de l'Arduino
- Brancher un fil entre la broche + du contrôleur et la broche V du port 7 de l'Arduino
- Moteur roue gauche sur les ports 8, 9, 10 et 11 de l'Arduino (détacher un groupe de 4 fils pour les broches IN et un groupe de 2 fils pour les broches - et +):
- Brancher un fil entre la broche IN1 du contrôleur et la broche S du port 8 de l'Arduino
- Brancher un fil entre la broche IN2 du contrôleur et la broche S du port 9 de l'Arduino
- Brancher un fil entre la broche IN3 du contrôleur et la broche S du port 10 de l'Arduino
- Brancher un fil entre la broche IN4 du contrôleur et la broche S du port 11 de l'Arduino
- Brancher un fil entre la broche - du contrôleur et la broche G du port 10 de l'Arduino
- Brancher un fil entre la broche + du contrôleur et la broche V du port 11 de l'Arduino

Brancher les moteurs pas-à-pas sur les contrôleurs. Marquer les moteurs droite et gauche afin de les différencier facilement lors du montage final.
Branchement du servo-moteur sur le port 3 : brancher le câble de façon à ce que le fil marron soit sur la broche G du port 3, le fil rouge sur la broche V et le fil orange sur la broche S
Attention pour les personnes ayant commandé le modèle suivant de shield :

Page 2 sur 13

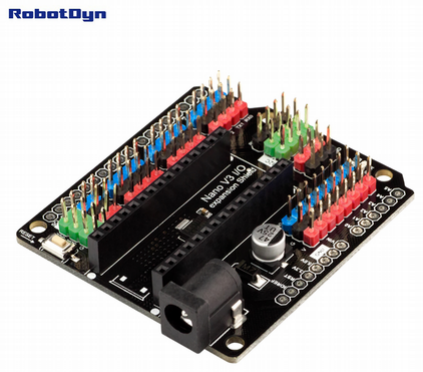
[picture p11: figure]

Il faut inverser les fils rouge et marron du servomoteur! Pour cela utiliser un petit tournevis plat et soulever légèrement le petit ergot au bout d'un des fils (rouge ou marron) puis tirer légèrement sur ce dernier, il devrait venir facilement. Faire de même avec le deuxième fil. Rebrancher les fils en les inversant par rapport à leur position initiale. Vous pourrez maintenant faire en sorte de respecter la consigne pour que « le fil marron soit sur la broche G du port 3, le fil rouge sur la broche V et le fil orange sur la broche S »
Branchement du module Bluetooth :
- Brancher le câble de l'interrupteur (détacher un groupe de 2 fils):
- Brancher un fil entre la broche G du port 12 de l'Arduino en face du fil noir de l'interrupteur
- Brancher un fil entre la broche V du port 12 de l'Arduino en face du fil rouge de l'interrupteur
- Brancher l'autre extrémité de l'interrupteur de manière à ce que le fil noir soit en face de la broche GND du module Bluetooth et le fil rouge en face de la broche +5V
- Brancher le module à l'Arduino (détacher un groupe de 2 fils) :
- Brancher un fil entre la broche RX du module Bluetooth et la broche S du port 13 de l'Arduino
- Brancher un fil entre la broche TX du module Bluetooth et la broche S du port 12 de l'Arduino

Découper les modèles de touches (disponibles sur https://github.com/Orange-OpenSource/oorobot/blob/master/doc/menu/menu.pdf) (https://github.com/Orange-OpenSource/oorobot/blob/master/doc/menu/menu.pdf) et les insérer dans le clavier, pour cela il faut sortir les touches (ça vient facilement en tirant dessus) puis enlever la partie transparente (vous pouvez utiliser une paire de ciseaux pour faire levier), placer les découpes et remettre en place les touches.
Télécharger et installer le programme Arduino IDE (https://www.arduino.cc/en/Main/Software) sur votre PC. Brancher l'Arduino avec un cable USB sur votre PC. Vous devriez voir apparaître dans le menu "Outils/Port" une nouvelle entrée (/dev/ttyUSBx sous Linux, COMx sous Windows). Sélectionner dans "Outils/Type de carte" le modèle "Arduino Nano" Télécharger le programme init-bluetooth (https://github.com/Orange-OpenSource/oorobot/blob/master/arduino/init-bluetooth) et l'ouvrir avec Arduino IDE. Téléverser le programme (2ème bouton en haut à gauche de l'interface) sur l'Arduino. Ce programme va configurer le module Bluetooth pour :
- Donner un nom au format "OoRoBoT-XXXX"
- Configurer le code PIN à 0000
- Configurer la vitesse de communication à 9600 bauds

Attendre quelques secondes puis vérifier que le robot est bien visible en Bluetooth. Vous pouvez utiliser le "moniteur série" (Menu "Options/Moniteur série") du programme Arduino IDE pour voir où en est la configuration du Bluetooth.
Télécharger le programme oorobot (https://github.com/Orange-OpenSource/oorobot/blob/master/arduino/oorobot) et l'ouvrir avec le programme Arduino IDE. Il faut installer les dépendances suivantes en allant dans le menu "Croquis/Inclure une bibliothèque/Gérer les bibliothèques" puis en cherchant les bibliothèques à installer :
- AccelStepper v1.57.1 by Mike McCauley
- LiquidCrystal I2C v1.1.2 by Frank de Brabander

Téléverser ensuite le programme oorobot sur l'Arduino. Ce programme va piloter tout le robot. Après le téléchargement il est temps de vérifier que le câblage est bien réalisé:
- Vérifier le branchement du clavier, un appui sur un bouton doit afficher des caractères sur l'écran LCD
- Vérifier le contraste de l'écran : ce dernier doit s'allumer au démarrage, par contre si vous ne voyez rien, pas de panique c'est peut-être tout simplement parce que le contraste est mal réglé. Pour changer ce

Page 3 sur 13 paramètre il suffit de tourner le petit potentiomètre derrière l'écran avec un tournevis cruciforme jusqu'à avoir un bon contraste entre l'affichage des caractères et le fond de l'écran
- Marquer le dessus du servomoteur : l'axe du moteur doit être sur la gauche du composant quand la partie mobile est devant vous. Vérifier que ce dernier bouge bien si vous appuyer sur les boutons lever/baisser le crayon
- Vérifier que les moteurs fonctionnent bien: lancer une commande "avance" pour vérifier que les moteurs tournent dans le bon sens, faire de même avec une commande "tourne à droite".
- Vérifier le sens de l'interrupteur : jouer avec le bouton de l'interrupteur pour voir dans quelle position il allume ou éteint le module Bluetooth. Veiller à noter ces états afin de bien positionner plus tard l'interrupteur sur le châssis.
- Vérifier que le module Bluetooth fonctionne : activer le Bluetooth sur votre téléphone/tablette et vérifier que vous pouvez bien vous appairez avec le robot (code PIN 0000). Si vous le pouvez vérifier ensuite que vous pouvez piloter le robot avec l'application Android fournie (voir plus bas)
Tout est OK ? Vous pouvez passer au montage des composants sur le châssis.

## Montage de la version en MDF

## Conseils

- Ne vissez pas les vis « à fond » pour fixer les composants dès le début. Placez votre première vis, faites quelques tours de tournevis pour que la vis ne sorte plus puis passer à la vis suivante. Quand toutes les vis sont en place pour tenir votre composant vous pouvez les serrez complétement sur le support.
- Vérifier bien que tous les composants fonctionnent avant de faire ce montage.

## Le montage

- Montez le support externe du crayon :

Page 4 sur 13

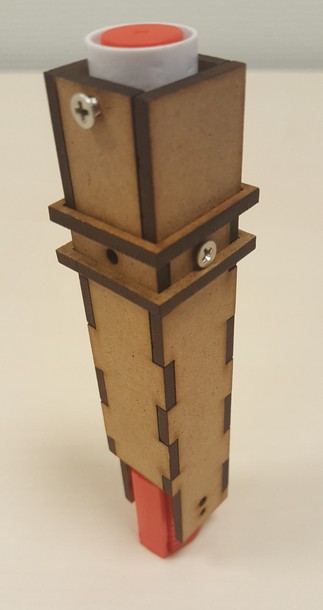
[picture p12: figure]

- Montez le support interne du crayon (ici version <= 13) :

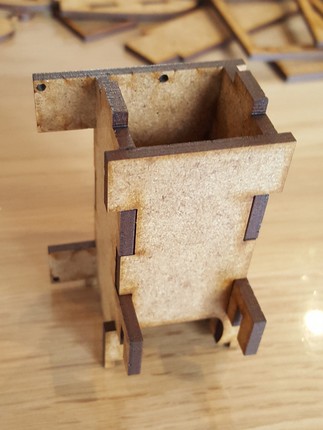
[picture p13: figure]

- Collez le support Arduino sur la partie dépassant du support interne du crayon (ici version > 13) :

Page 5 sur 13

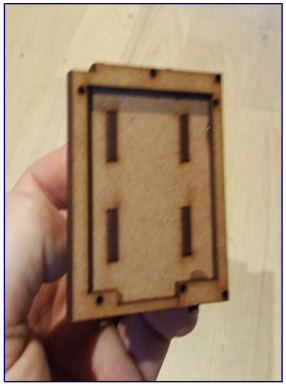
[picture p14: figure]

- Placez l'interrupteur (en ayant auparavant dévissé le « cache » fourni) en réutilisant les vis (attention à bien retenir leur sens pour respecter les positions arrêt/marche) :

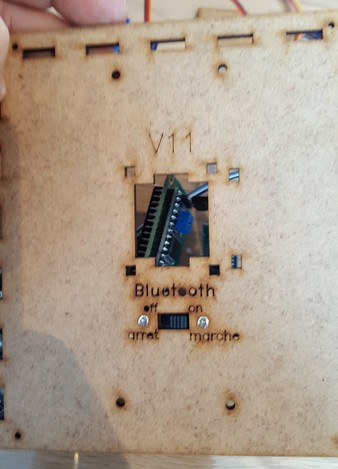
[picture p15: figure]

- Fixez le servomoteur sur son support (utilisez les vis fournies avec le servomoteur), bien faire attention au sens de rotation, l’axe doit être sur la droite comme sur la photo ci-dessous :

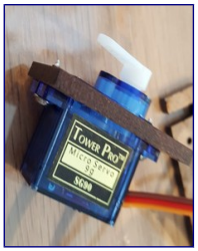
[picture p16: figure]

- Placez le support du servomoteur sur la plaque de fond :

Page 6 sur 13

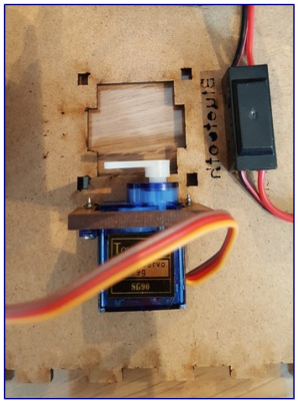
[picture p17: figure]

- Rabaissez (ou coupez) les broches qui sont au-dessus de l’Arduino pour faciliter le montage des côtés :

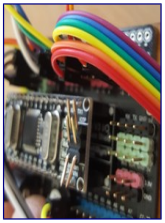
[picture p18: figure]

- Vissez l’Arduino sur le support Arduino qui est lui-même collé sur le support interne du crayon (ici version <= 13):
- Fixez le clavier :

Page 7 sur 13

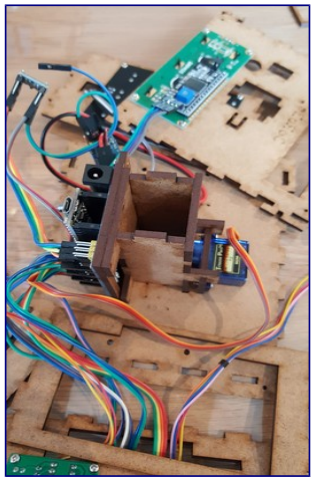
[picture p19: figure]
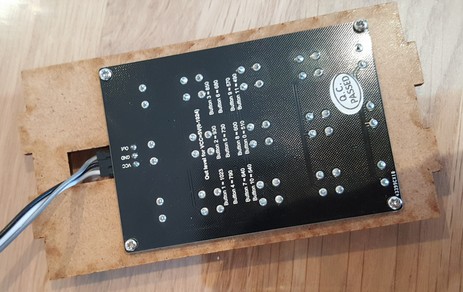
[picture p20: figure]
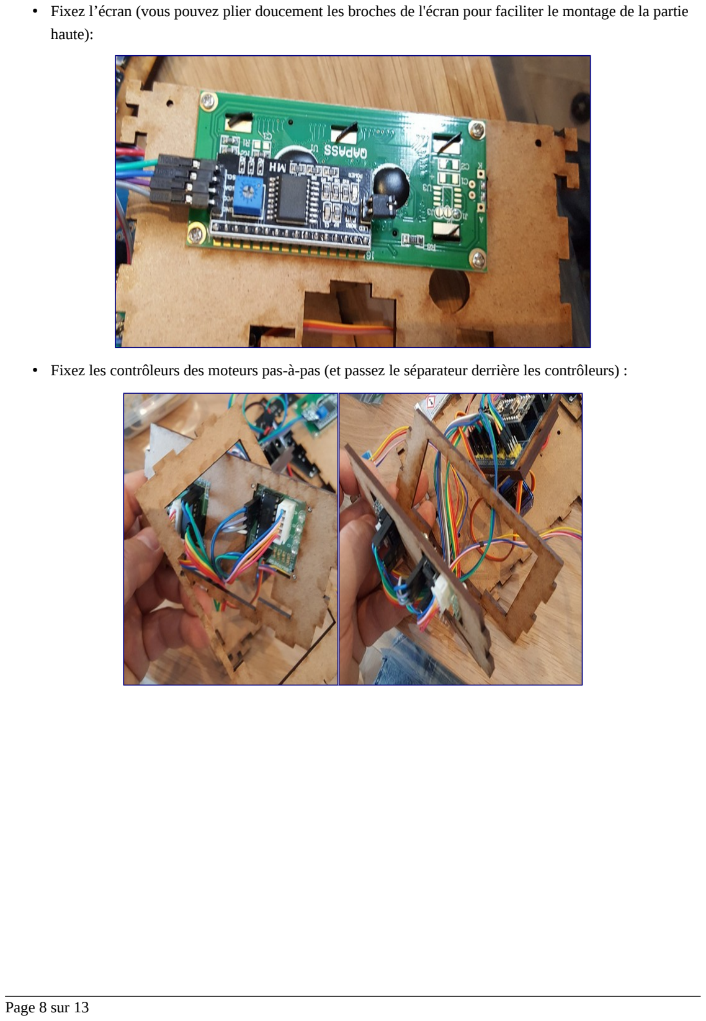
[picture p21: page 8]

- Fixez l’écran (vous pouvez plier doucement les broches de l'écran pour faciliter le montage de la partie haute):
- Fixez les contrôleurs des moteurs pas-à-pas (et passez le séparateur derrière les contrôleurs) :

Page 8 sur 13

- Fixez les moteurs sur les plaques des côtés (vis M3) et placez les rondelles autour des moyeux :

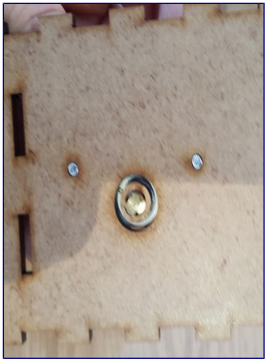
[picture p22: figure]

- Collez des élastiques autour des roues
- Encastrez les roues (en tenant bien l’arrière des moteurs pour que les vis ne sortent pas) et ajoutez une des formes de "bloqueur" (petit ou grand selon ce que vous préférez) :

Page 9 sur 13

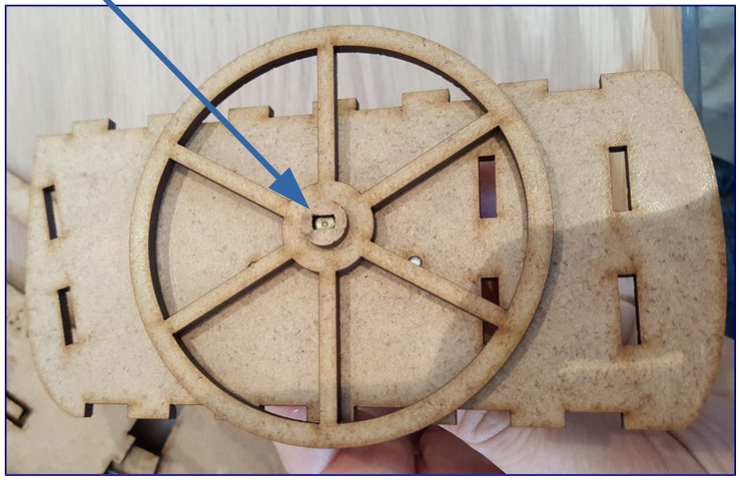
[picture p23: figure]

- Encastrez le support des contrôleurs des moteurs pas-à-pas, le séparateur et le support du clavier entre les deux côtés du châssis (utilisez de la colle pour maintenir les côtés au besoin). Attention : comme montré ci-dessous il faut que les fils de l'écran sortent par le haut du montage :

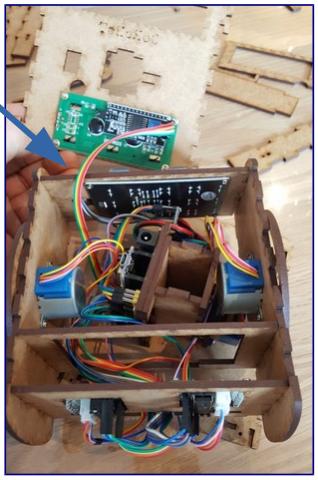
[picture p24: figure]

- Encastrez les côtés sur le fond du châssis

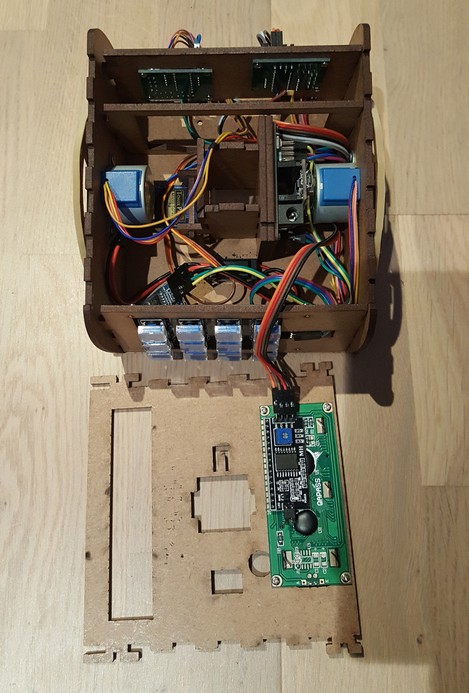
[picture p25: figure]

- Attention : avant de continuer le montage, je vous conseil de vérifier que tous les composants fonctionne toujours bien ! Il se peut que des fils sortent des broches durant les manipulations précédentes.

Page 10 sur 13

- Glissez le fond du boitier à piles entre le support des contrôleurs de moteurs pas-à-pas avec la séparation :

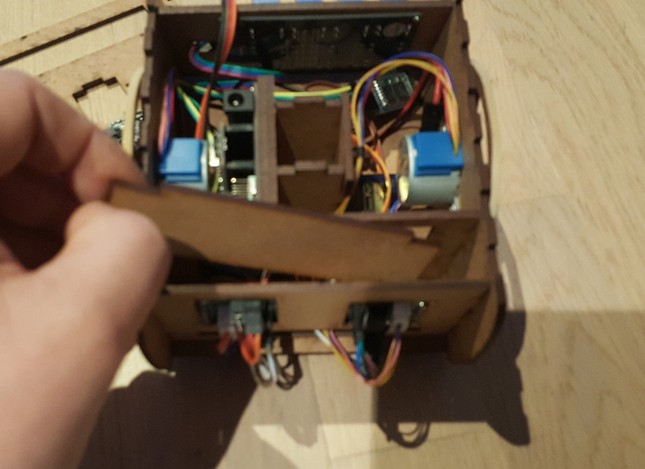
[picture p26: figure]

- Entrez cette pièce dans l'encoche visible sous les contrôleurs de moteur pas-à-pas :

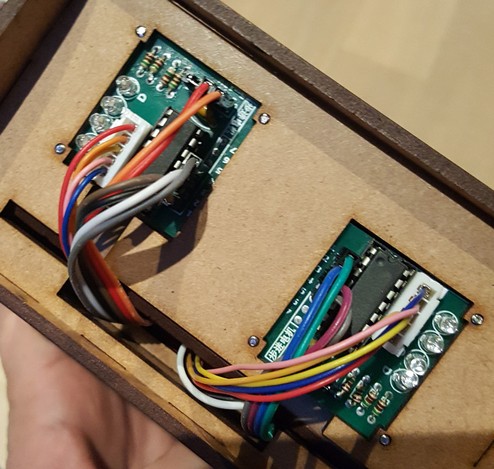
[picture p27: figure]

- Poussez (par le haut du robot) sur cette pièce, elle devrait s'encastrer pour se positionner parallèlement au bas du robot (Faire en sorte que des fils ne gênent pas cette manipulation)

Page 11 sur 13

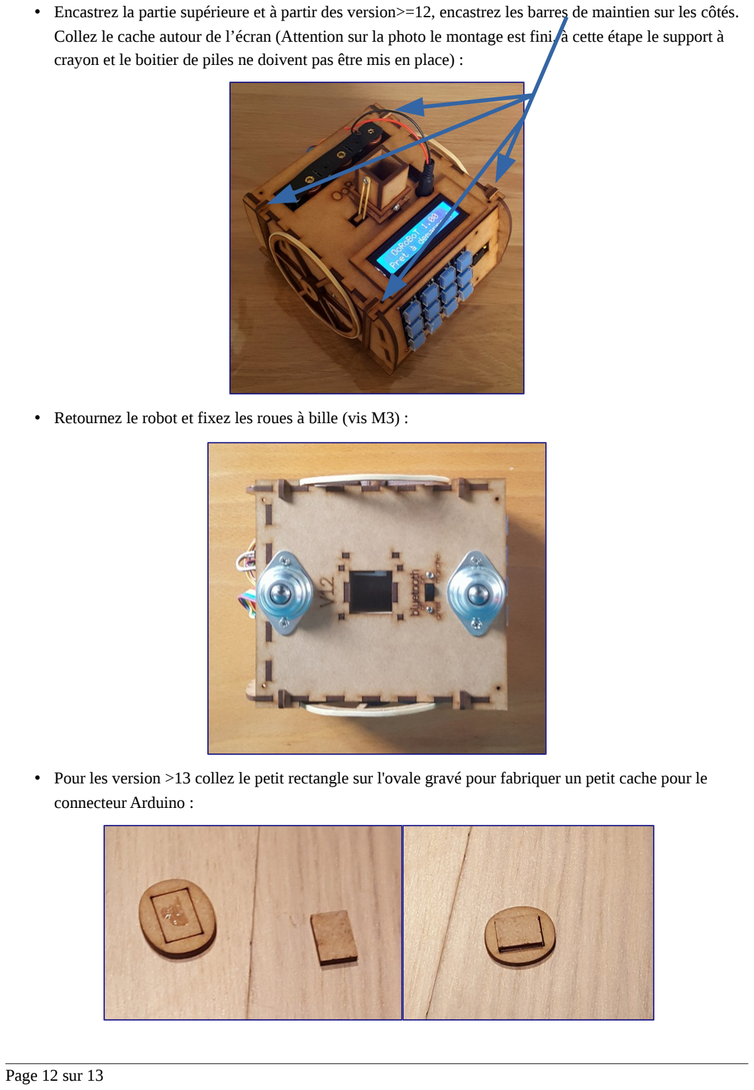
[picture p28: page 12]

- Encastrez la partie supérieure et à partir des version>=12, encastrez les barres de maintien sur les côtés. Collez le cache autour de l’écran (Attention sur la photo le montage est fini, à cette étape le support à crayon et le boitier de piles ne doivent pas être mis en place) :
- Retournez le robot et fixez les roues à bille (vis M3) :
- Pour les version >13 collez le petit rectangle sur l'ovale gravé pour fabriquer un petit cache pour le connecteur Arduino :

Page 12 sur 13

Et pour terminer :
- Insérer le support de crayon externe dans le robot, vous pouvez mettre un élastique entre le dessus du robot et ce support pour avoir une meilleure pression sur le crayon
- Calibrer votre robot via le menu "paramètres" (appui long sur le bouton au milieu de la colonne la plus à droite du clavier):
- Le nombre de pas que les moteurs doivent faire pour effectuer un 1/4 de tour : pour cela, avec le clavier entrez le programme "tourner à droite" 4 fois et lancez le. Si le robot n'a pas fait exactement un tour, rentrez dans le menu "paramètres" et changez le nombre de pas, appuyez sur le bouton start, vous reviendrez sur votre programme que vous pourrez relancer pour affiner votre réglage
- Le nombre de pas que les moteurs doivent faire pour avancer de 10 cm, procédez comme pour le réglage d'un tour complet. Vous pouvez utiliser la fonction de dessin avec un crayon pour mesurer la précision du robot.

Page 13 sur 13

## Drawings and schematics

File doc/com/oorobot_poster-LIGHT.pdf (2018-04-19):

## un robot éducatif simple à construire

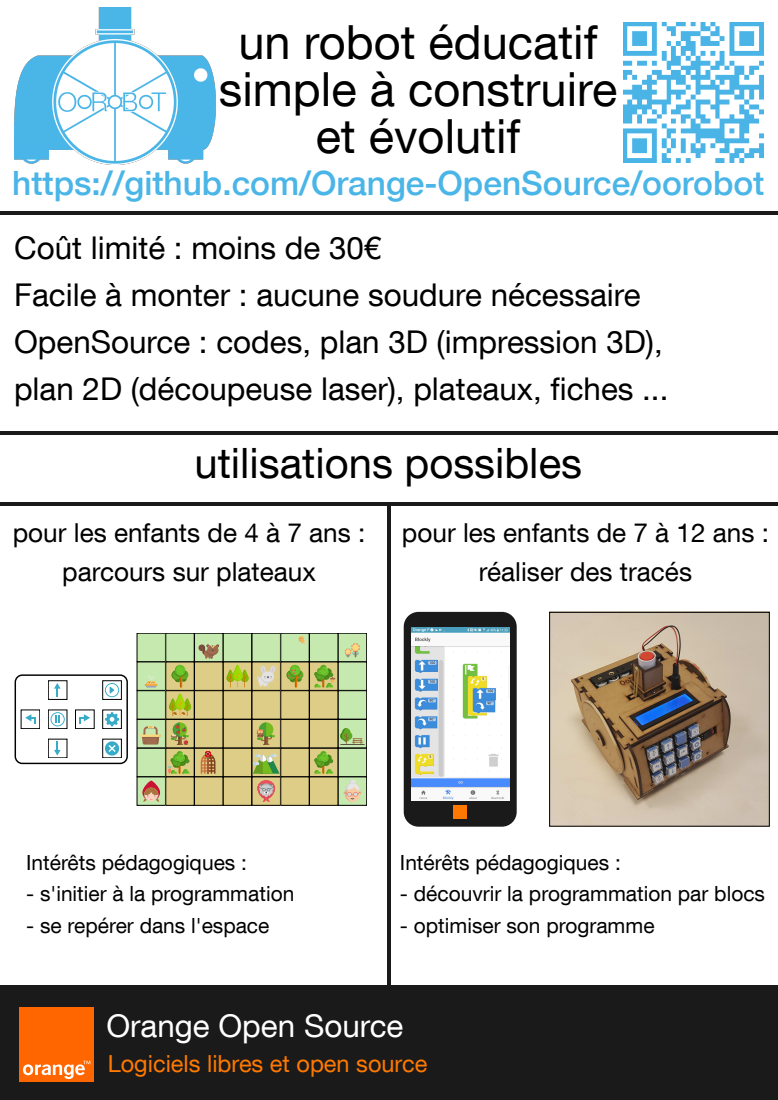
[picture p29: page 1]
et évolutif; utilisations possibles

https://github.com/Orange-OpenSource/oorobot

Coût limité : moins de 30€
Facile à monter : aucune soudure nécessaire
OpenSource : codes, plan 3D (impression 3D),
plan 2D (découpeuse laser), plateaux, fiches ...

pour les enfants de 4 à 7 ans :
parcours sur plateaux

pour les enfants de 7 à 12 ans :

réaliser des tracés

Intérêts pédagogiques :
- s'initier à la programmation
- se repérer dans l'espace

- découvrir la programmation par blocs
- optimiser son programme

Orange Open Source
Logiciels libres et open source

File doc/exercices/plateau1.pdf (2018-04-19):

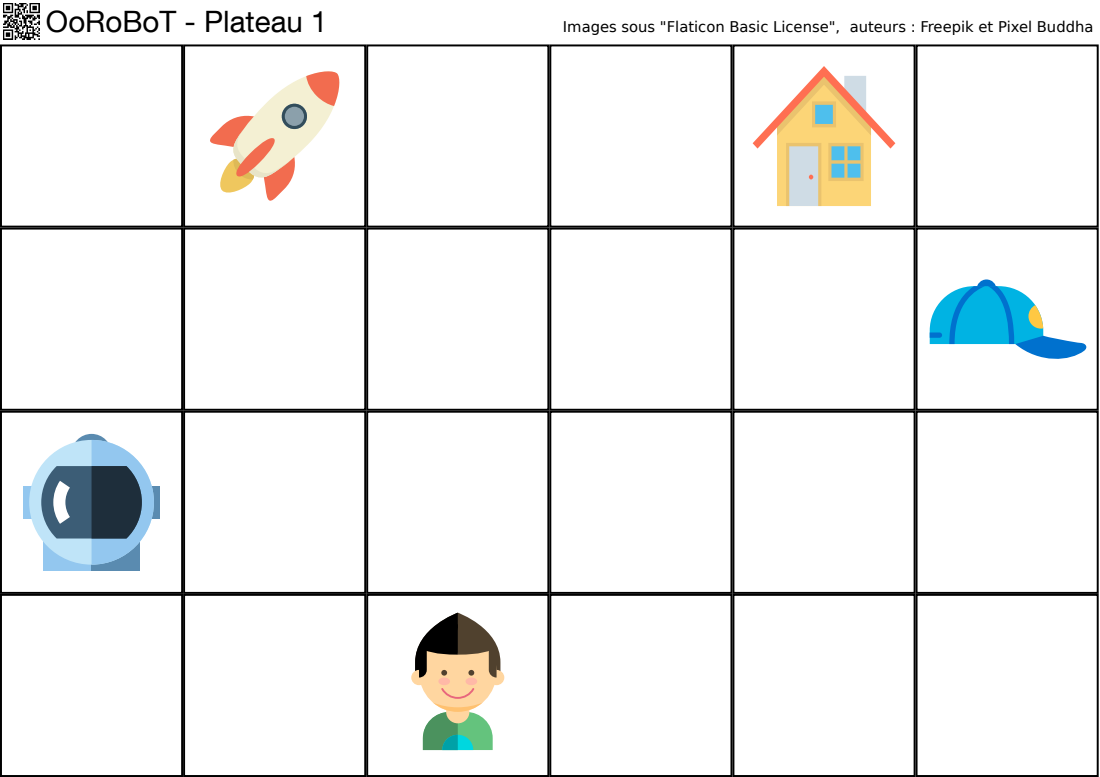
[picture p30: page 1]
OoRoBoT - Plateau 1; Images sous "Flaticon Basic License", auteurs : Freepik et Pixel Buddha

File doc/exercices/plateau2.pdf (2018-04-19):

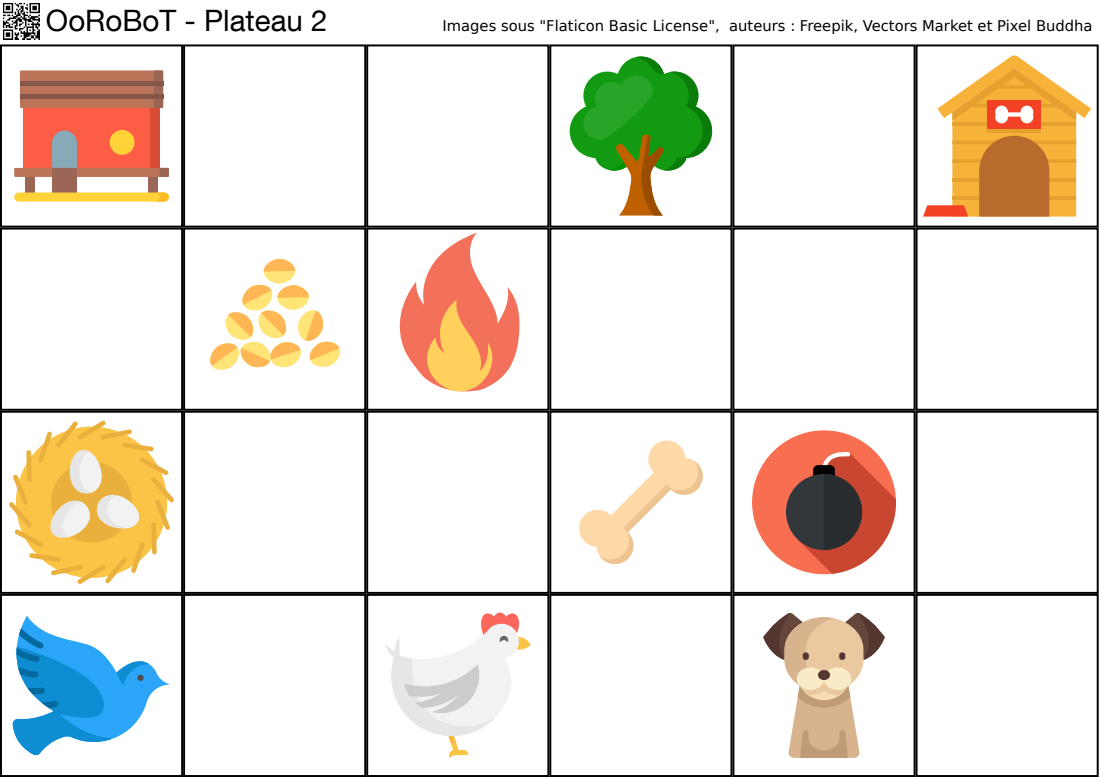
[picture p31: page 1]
OoRoBoT - Plateau 2; Images sous "Flaticon Basic License", auteurs : Freepik, Vectors Market et Pixel Buddha

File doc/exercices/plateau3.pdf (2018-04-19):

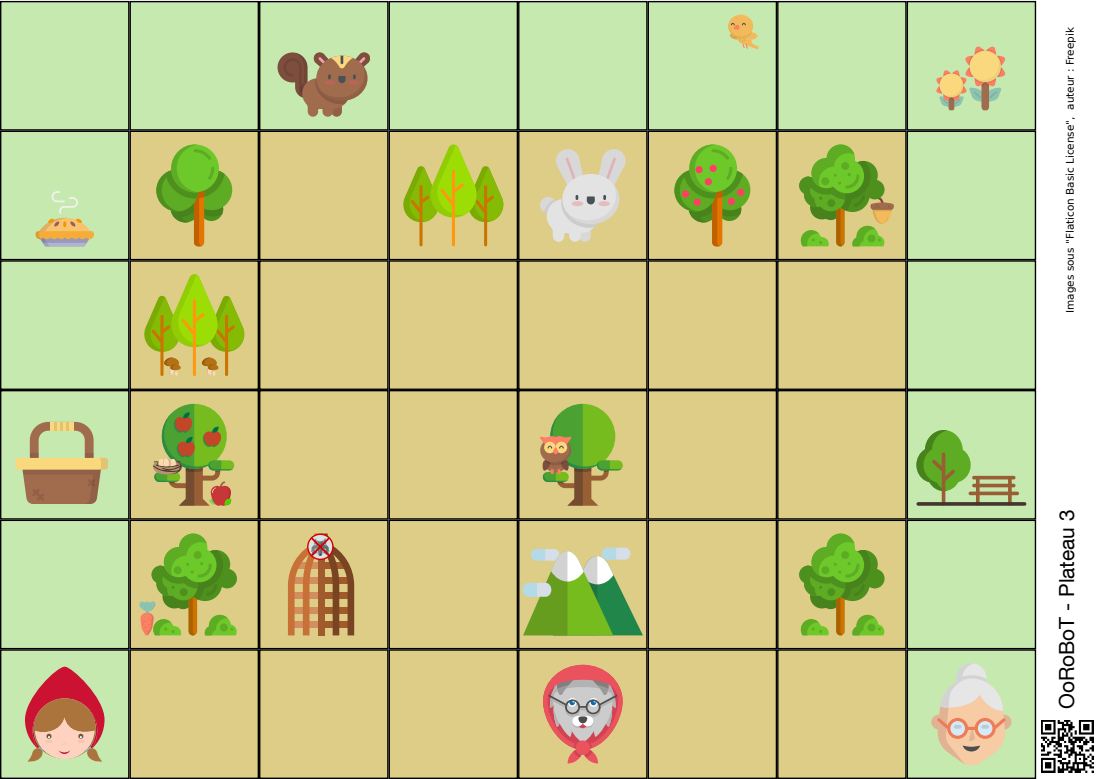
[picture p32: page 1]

OoRoBoT - Plateau 3 Images sous "Flaticon Basic License", auteur : Freepik

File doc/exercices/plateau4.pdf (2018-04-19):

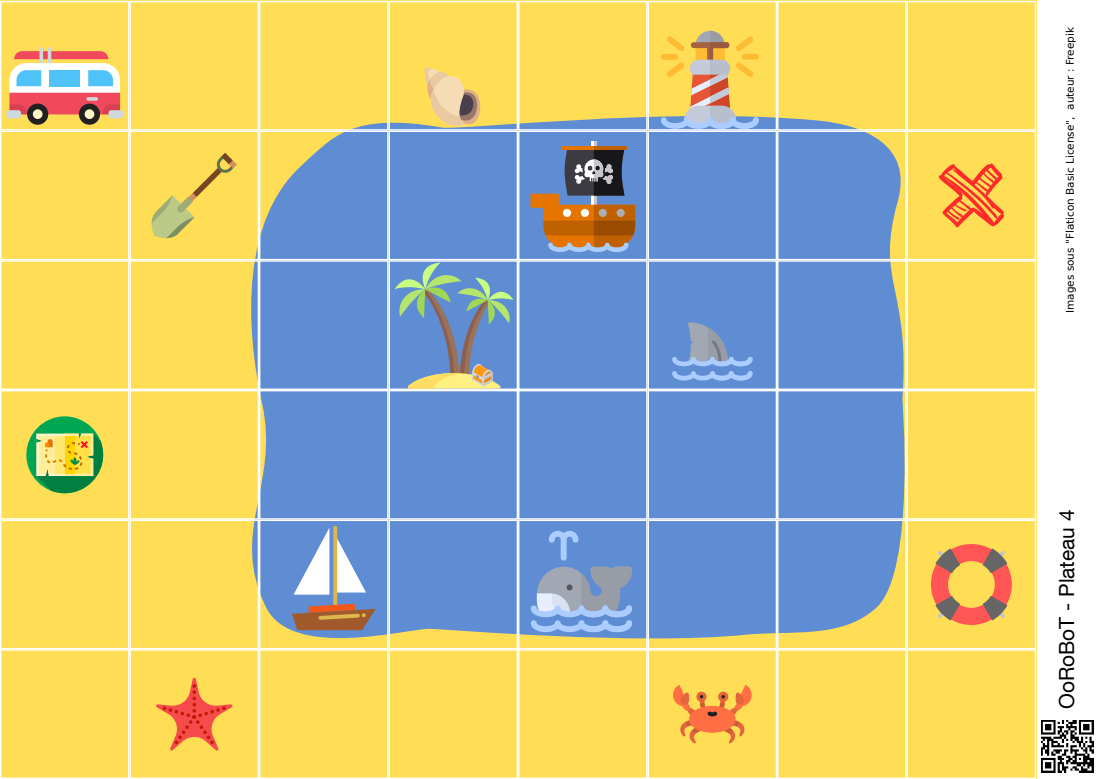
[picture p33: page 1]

OoRoBoT - Plateau 4 Images sous "Flaticon Basic License", auteur : Freepik

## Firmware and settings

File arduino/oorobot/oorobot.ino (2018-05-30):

/*
   OoRoBoT code

   Get the following libraries (using the Arduino IDE library manager)
  - **AccelStepper** v1.57.1 by Mike McCauley
  - **LiquidCrystal I2C** v1.1.2 by Frank de Brabander
 
*/
#include <EEPROM.h>
#include <Wire.h>
#include <LiquidCrystal_I2C.h>
#include <AccelStepper.h>
#include <Servo.h>
#include "charset.h"
#include "buttons.h"


#define OOROBOT_VERSION "1.1.1"

#define SCREEN_TIMEOUT 25

// On some step motors direction may be inverted
// define this symbol to invert the motors direction
#define INVERT_DIRECTION
#define MAX_COMMANDS 512
#define MAX_LOOPS 10

// define this symbol to add bluetooth support
#define HAVE_BLUETOOTH

#ifdef HAVE_BLUETOOTH
# include <SoftwareSerial.h>
# define RxD 12
# define TxD 13
SoftwareSerial BTSerie(RxD, TxD);
#endif

// motor pins
#define motorPin1  4     // IN1 on the ULN2003 driver 1
#define motorPin2  5     // IN2 on the ULN2003 driver 1
#define motorPin3  6     // IN3 on the ULN2003 driver 1
#define motorPin4  7     // IN4 on the ULN2003 driver 1

#define motorPin5  8     // IN1 on the ULN2003 driver 2
#define motorPin6  9     // IN2 on the ULN2003 driver 2
#define motorPin7  10    // IN3 on the ULN2003 driver 2
#define motorPin8  11    // IN4 on the ULN2003 driver 2

// Menu index
#define START_MENU 0
#define SETTINGS_MENU 1
#define CTRL_MENU 2
#define RUNNING_MENU 3
#define OFF_MENU 4

#define MAX_STEPPER_SPEED 900
#define MIN_STEPPER_SPEED 200
#define WHEEL_SPACING_MM 132

int stepperSpeed = MIN_STEPPER_SPEED;

// Initialize with pin sequence IN1-IN3-IN2-IN4 for using the AccelStepper with 28BYJ-48
AccelStepper stepper1(AccelStepper::HALF4WIRE, motorPin1, motorPin3, motorPin2, motorPin4);
AccelStepper stepper2(AccelStepper::HALF4WIRE, motorPin5, motorPin7, motorPin6, motorPin8);

Servo penServo;

// The I2C LCD object
LiquidCrystal_I2C lcd(0x27, 16, 2);

struct Params {
  int stepCm;
  int turnSteps;
  int lineSteps;
};

int stepDelay = 800;
int steps1 = 0; // keep track of the step count for motor 1
int steps2 = 0; // keep track of the step count for motor 2
int isMoving = false;

char buttonsMap[] = {
  'L', 'G', 's', 'C', 0, 'R', 0, 'U', 'P', 'D', '|', '!',
  '-',  0, 'S', 'A', 0, '+', 0,  0,   0,   0,  0, 0
};

Params params = {140, 1430, 100};
int previousMenu = CTRL_MENU;
int selectedMenu = START_MENU;
char cmd[MAX_COMMANDS + 1] = {};
int loopCounter[MAX_LOOPS] = {};
int loopPointer[MAX_LOOPS] = {};
int loopIndex=0;
int currentRadius=0;
boolean reverseOrientation=false;

unsigned char cmd_l = 0;
int changeDisplay = 1;
long lastChangeDisplay = 0;
unsigned int selectedLine = 0;
short commandLaunched = 0;
short consecutive_numbers = 0;
#define MAX_CONSECUTIVE_NUMBERS 3
short num_of_cmd = 0;
short max_num_cmd = 0;
long startMovement=0;



void moveServo(int angle) {
  penServo.attach(3);
  penServo.write(angle);
  delay(200);
  penServo.detach();
}


void setup() {
  Serial.begin(9600);
  loadParams();
  setupButtons();
  Serial.println(F("Setup"));

  lcd.init();
  lcd.backlight();
  lcd.createChar(1, up);
  lcd.createChar(2, down);
  lcd.createChar(4, right);
  lcd.createChar(3, left);
  lcd.createChar(5, pause);
  lcd.createChar(6, bullet);
  lcd.createChar(7, agrave);

  // stepper motors init
  stepper1.setMaxSpeed(1000);
  stepper1.move(1);

  stepper2.setMaxSpeed(1000);
  stepper2.move(-1);

  moveServo(5);

  // Bluetooth module init
#ifdef HAVE_BLUETOOTH
  pinMode(RxD, INPUT);
  pinMode(TxD, OUTPUT);
  BTSerie.begin(9600);
#endif
}

void loop() {
  long currentTime = millis();
  int buttonId = getPressedButton();
  char button = 0;
  if (buttonId >= 0) {
    button = buttonsMap[buttonId];
    if (button != 0) {
      actionButtonForScreen(button);
    }
  } else {
#ifdef HAVE_BLUETOOTH
    while (BTSerie.available()) {
      selectedMenu = CTRL_MENU;
      button = BTSerie.read();
      //Serial.println(button);
      if (button != 0) {
        actionButtonForScreen(button);
      }
    }
#endif
    while (Serial.available()) {
      selectedMenu = CTRL_MENU;
      button = Serial.read();
      //Serial.println(button);
      if (button != 0) {
        actionButtonForScreen(button);
      }
    }
  }

  if (isMoving) {
    if (isCommandTerminated()) {
      Serial.println(F("step delay"));
      if (! launchNextCommand()) {
        Serial.println(F("program terminated"));
        isMoving = false;
        disableMotors();
        lcd.clear();
        lcd.setBacklight(HIGH);
        lcd.print(F("fin !"));
#ifdef HAVE_BLUETOOTH
        BTSerie.println(F("fin !"));
#endif
        delay(1000);
        selectedMenu = CTRL_MENU;
        changeDisplay = 1;
      }
    }
  }
  updateScreen();

  // Screen off after 4s
  if (currentTime > lastChangeDisplay + SCREEN_TIMEOUT * 1000) {
    if (selectedMenu != OFF_MENU) {
      previousMenu = selectedMenu;
      selectedMenu = OFF_MENU;
      changeDisplay = 1;
    }
  }

}



void actionButtonForScreen(char button) {

  if (selectedMenu == START_MENU) {
    selectedMenu = CTRL_MENU;
    changeDisplay = 1;
  } else if (selectedMenu == CTRL_MENU) {
    changeDisplay = 1;
    Serial.print(F("New char : "));
    Serial.println(button);
    if ( button > 47  && button < 58) // it's a number
    {
      consecutive_numbers++;
      if (consecutive_numbers > MAX_CONSECUTIVE_NUMBERS)
      {
        Serial.println(F("number too hight"));
        return;
      }
      else
      {
        cmd[cmd_l++] = button;
        return;
      }
    }
    else
    {
      switch (button) {
        case 'S':
          selectedMenu = SETTINGS_MENU;
          changeDisplay = 1;
          break;
        case 'G':
          stepDelay = 800;
          selectedMenu = RUNNING_MENU;
          isMoving = true;
          commandLaunched = 0;

          max_num_cmd = num_of_cmd;
          num_of_cmd = 0;
          launchNextCommand();

          break;
        case 'A':
          cmd_l = 0;
          commandLaunched = 0;
          num_of_cmd = 0;
          break;
        case 'C':
          while (cmd_l > 0  &&  cmd[cmd_l - 1] > 47  && cmd[cmd_l - 1]  < 58)
          {
            cmd_l--;  //remove all number;
          }
          if (cmd_l > 0) {
            cmd_l--;
            num_of_cmd--;
          }
          break;
        case 'B' :
        case 'a' :
        case 'c' : 
        case 'r' :
        case 'E' :
        case 'U' :
        case 'D' :
        case 'L' :
        case 'R' :
        case 'W' :
        case '!' :
        case '|' :
        case 'P' :
          if (cmd_l < MAX_COMMANDS) {
            cmd[cmd_l++] = button;
            num_of_cmd++;
          } else {
            Serial.println(F("too many commands"));
          }
          break;
        case 0 :
        case '+' :
        case '-' :
        case 's' :
          changeDisplay = 0;
          break;
        default:
          Serial.println(F("Unknown Command"));
#ifdef HAVE_BLUETOOTH
          BTSerie.println(F("Unknown Command"));
#endif
          break;
      }
      consecutive_numbers = 0;
    }
  } else if (selectedMenu == SETTINGS_MENU) {
    actionButtonForSettingsScreen(button);
  } else if (selectedMenu == RUNNING_MENU) {
    disableMotors();
    isMoving = false;
    lcd.clear();
    lcd.setBacklight(HIGH);
    lcd.print(F("Arret!"));
    delay(1000);
    selectedMenu = CTRL_MENU;
    changeDisplay = 1;
  } else if (selectedMenu == OFF_MENU) {
    selectedMenu = previousMenu;
    changeDisplay = 1;
  }
}

void actionButtonForSettingsScreen(char button) {
  changeDisplay = 1;
  switch (button) {
    case 'U':
      selectedLine--;
      selectedLine = selectedLine % 3;
      break;
    case 'D':
      selectedLine++;
      selectedLine = selectedLine % 3;
      break;
    case 'R':
      if (selectedLine == 0) {
        params.stepCm++;
      } else if (selectedLine == 1) {
        params.turnSteps++;
      } else {
        params.lineSteps++;
      }
      break;
    case '+':
      if (selectedLine == 0) {
        params.stepCm += 10;
      } else if (selectedLine == 1) {
        params.turnSteps += 10;
      } else {
        params.lineSteps += 10;
      }
      break;
    case 'L':
      if (selectedLine == 0) {
        params.stepCm--;
      } else if (selectedLine == 1) {
        params.turnSteps--;
      } else {
        params.lineSteps--;
      }
      break;
    case '-':
      if (selectedLine == 0) {
        params.stepCm -= 10;
      } else if (selectedLine == 1) {
        params.turnSteps -= 10;
      } else {
        params.lineSteps -= 10;
      }
      break;
    case 's':
    case 'G':
      saveParams();
      selectedMenu = CTRL_MENU;
      break;
    case 'C':
      loadParams();
      selectedMenu = CTRL_MENU;
      break;
  }
}

void updateScreen() {
  if (changeDisplay) {
    if (selectedMenu == START_MENU) {
      //lcd.setBacklight(HIGH);
      lcd.display();
      lcd.setCursor(0, 0);
      lcd.print(" OoRoBoT  " OOROBOT_VERSION);
      lcd.setCursor(0, 1);
      lcd.print(F("Pret \7 demarrer!"));
#ifdef HAVE_BLUETOOTH
      BTSerie.println("OoRoBoT " OOROBOT_VERSION);
      BTSerie.println(F("En attente de commandes"));
#endif
      previousMenu = CTRL_MENU;
      selectedMenu = CTRL_MENU;
    } else if (selectedMenu == CTRL_MENU) {
      lcd.setBacklight(HIGH);
      cmd[cmd_l] = 0;
#ifdef HAVE_BLUETOOTH
      BTSerie.println(cmd);
#endif
      lcd.clear();
      lcd.setCursor(0, 0);
      for (char i = 0 ; i < cmd_l ; i++) {
        if (i == 16) {
          lcd.setCursor(0, 1);
        }
        lcd.print(commandToDisplay(cmd[i]));
      }
    } else if (selectedMenu == SETTINGS_MENU) {
      lcd.setBacklight(HIGH);
      lcd.clear();
      int cm = params.stepCm / 10;
      int mm = params.stepCm - 10 * cm;
      int currentLine=selectedLine;
      int stepIdx=0;
      int turnIdx=1;
      int lineIdx=2;
      Serial.print("selectedLine:");
      Serial.println(selectedLine);
      if (selectedLine==2) {
        stepIdx=2;
        turnIdx=2;
        lineIdx=0;  
      }
      if (stepIdx<2) {
        lcd.setCursor(0, stepIdx);
        lcd.print(F(" Distance:"));
        lcd.print(cm);
        lcd.print(F("."));
        lcd.print(mm);
        lcd.print(F("cm"));
      }      
      if (turnIdx<2) {
        lcd.setCursor(0, turnIdx);
        lcd.print(F(" 1/4Tour:"));
        lcd.print(params.turnSteps);
        lcd.print(F("pas"));
      }
      if (lineIdx<2) {
        lcd.setCursor(0, lineIdx);
        lcd.print(F(" 1cm:"));
        lcd.print(params.lineSteps);
        lcd.print(F("pas"));
      }
      
      lcd.setCursor(0, selectedLine%2);
      lcd.print("\6");
#ifdef HAVE_BLUETOOTH
      if (selectedLine == 0) {
        BTSerie.print(F("Distance:"));
        BTSerie.print(cm);
        BTSerie.print(F("."));
        BTSerie.print(mm);
        BTSerie.println(F("cm"));
      } else {
        BTSerie.print(F("1/4Tour:"));
        BTSerie.print(params.turnSteps);
        BTSerie.println(F("pas"));
      }
#endif

    } else if (selectedMenu == CTRL_MENU) {
      lcd.setBacklight(HIGH);
    } else if (selectedMenu == OFF_MENU) {
      lcd.setBacklight(LOW);
    }
    lastChangeDisplay = millis();
  }
  changeDisplay = 0;
}

char commandToDisplay(char c) {
  switch (c) {
    case 'U':
      return 1;
      break;
    case 'D':
      return 2;
      break;
    case 'L':
      return 3;
      break;
    case 'R':
      return 4;
      break;
    case 'P':
      return 5;
      break;
    default:
      return c;
  }
}

int startLoop=-1;
int remainingLoop=0;

boolean launchNextCommand() {
  if (commandLaunched >= cmd_l) {
    return false;
  } else {
    disableMotors();
    lcd.clear();
    if (stepDelay>100) {
      lcd.setBacklight(HIGH);
      lcd.print((num_of_cmd + 1));
      lcd.print(F(" sur "));
      lcd.print(max_num_cmd);
      lcd.print(F(" : "));
      lcd.print(commandToDisplay(cmd[commandLaunched]));
    }
#ifdef HAVE_BLUETOOTH
    BTSerie.println(cmd[commandLaunched]);
#endif
    Serial.print(F("etape "));
    Serial.print((num_of_cmd + 1));
    Serial.print(F(" sur "));
    Serial.print(max_num_cmd);
    Serial.print(F(" : "));
    Serial.println(cmd[commandLaunched]);

    num_of_cmd++;
    delay(stepDelay);
    lcd.setBacklight(LOW);
    
    enableMotors();

    char command = cmd[commandLaunched];
    short stepSize = getStepSize(cmd, &commandLaunched);

    Serial.print(F("stepSize :"));
    Serial.println(stepSize);
    switch (command) {
      case 'W':
        Serial.println(F("set waiting step delay"));
        stepDelay=stepSize;
        break;
      case 'U':
        Serial.println(F("stepForward"));
        stepForward(stepSize);
        break;
      case 'D':
        Serial.println(F("stepBackward"));
        stepBackward(stepSize);
        break;
      case 'L':
        Serial.println(F("turnLeft"));
        turnLeft(stepSize);
        break;
      case 'R':
        Serial.println(F("turnRight"));
        turnRight(stepSize);
        break;
      case 'P':
        Serial.println(F("pause"));
        delay(stepSize);
        break;
      case '!' :
        Serial.println(F("pen down"));
        moveServo(0);
        break;
      case '|' :
        Serial.println(F("pen up"));  
        moveServo(30);
        break;
      case 'c' :
        currentRadius = stepSize;
        break;
      case 'r':
        if (stepSize==1) {
          reverseOrientation=true;
        } else {
          reverseOrientation=false;         
        }
        break;
      case 'a' :
        Serial.println(F("doCircle"));
        doCircle(currentRadius, stepSize, reverseOrientation);
        break;
      case 'B':
        Serial.println(F("begin loop"));
        if (loopIndex>=MAX_LOOPS) {
          Serial.println(F("too many loops included"));
        } else {
          loopCounter[loopIndex] = stepSize;
          loopPointer[loopIndex] = commandLaunched;
          loopIndex++;
          startLoop=commandLaunched;
          remainingLoop=stepSize;
        }
        break;
      case 'E':
        Serial.println(F("end loop"));
        if (loopCounter[loopIndex-1]>1) {
          commandLaunched=loopPointer[loopIndex-1];
          loopCounter[loopIndex-1]--;
        } else {
          if (loopIndex>0) {
            loopIndex--;
          }
        }
        break;
    }
    commandLaunched++;
    return true;
  }
}

short getStepSize(char* cmd,  short* commandLaunched)
{
  char command = cmd[*commandLaunched];
  int stepsize = 0;
  for (short i = 0; i < MAX_CONSECUTIVE_NUMBERS ; i++)
  {
    if (*commandLaunched + 1 < MAX_COMMANDS - 1 )
    {
      if (cmd[*commandLaunched + 1] > 47 && cmd[*commandLaunched + 1] < 58)
      {
        stepsize = stepsize * 10 + cmd[*commandLaunched + 1 ] - 48;
        *commandLaunched = *commandLaunched + 1;
      }
    }
  }

  if (stepsize == 0)
  {
    switch (command) {
      case 'W':
        stepsize = stepDelay;
        break;
      case 'U':
      case 'D':
        stepsize = params.stepCm; //10cm
        break;
      case 'L':
      case 'R':
        stepsize = 90;  // 90°;
        break;
      case 'P':
        stepsize=stepDelay*2;
        break;
    }
  }

  return stepsize;

}

boolean isCommandTerminated() {
  /*
  int diff = (millis() - startMovement);
  if (diff>=100) {
    startMovement=millis();
    stepperSpeed+=100;
    if (stepperSpeed>MAX_STEPPER_SPEED) {
      stepperSpeed=MAX_STEPPER_SPEED;
    } else {
      Serial.print(F("speed:"));
      Serial.println(stepperSpeed);
      stepper2.setSpeed(stepperSpeed);
      stepper1.setSpeed(stepperSpeed);
    }
  }
  */
  stepper2.setSpeed(MAX_STEPPER_SPEED);    
  stepper1.setSpeed(MAX_STEPPER_SPEED);

  steps1 = stepper1.distanceToGo();
  steps2 = stepper2.distanceToGo();
  //Serial.println(steps1);
  stepper1.runSpeedToPosition();
  stepper2.runSpeedToPosition();

  if (steps1 == 0 && steps2 == 0) {
    return true;
  } else {
    return false;
  }
}

void enableMotors() {
  stepper1.setCurrentPosition(0);
  stepper2.setCurrentPosition(0);
  stepper1.enableOutputs();
  stepper2.enableOutputs();
}

void disableMotors() {
  stepper1.stop();
  stepper2.stop();
  stepper1.disableOutputs();
  stepper2.disableOutputs();
}

void doCircle(float radius, float angle, boolean reverseOrientation){
  isMoving = true;
  startMovement=millis();
  //AAW10r1c50a90G
  //AAW10r0c200a45G
  float lenght_big_arc, lenght_small_arc;
  float steps_big_arc, steps_small_arc;
  float speed_big_arc, speed_small_arc;

  lenght_big_arc = 2 * PI * (radius + (WHEEL_SPACING_MM/2)) * (angle / 360);
  steps_big_arc = round(lenght_big_arc * params.stepCm / 10);
  speed_big_arc = MAX_STEPPER_SPEED;

  lenght_small_arc = 2 * PI * (radius - (WHEEL_SPACING_MM/2)) * (angle / 360);
  steps_small_arc = round(lenght_small_arc * params.stepCm / 10);
  speed_small_arc = abs((steps_small_arc*speed_big_arc)/steps_big_arc);

  if (reverseOrientation) {
    stepper2.move(-steps_big_arc);
    stepper2.setSpeed(speed_big_arc);
    stepper1.move(-steps_small_arc);
    stepper1.setSpeed(speed_small_arc);
  } else {
    stepper1.move(steps_big_arc);
    stepper1.setSpeed(speed_big_arc);
    stepper2.move(steps_small_arc);
    stepper2.setSpeed(speed_small_arc);
  }

}

void stepForward(short distance) {
  isMoving = true;
  startMovement=millis();
  stepperSpeed = MIN_STEPPER_SPEED;

  int target = (int)  (((float)params.stepCm / 10.0f) * ((float)distance * (float)params.lineSteps / 100.0f));
#ifdef INVERT_DIRECTION
  target = target * -1;
#endif

  stepper1.move(-target);
  stepper2.move(target);
}

void stepBackward(short distance) {
  isMoving = true;
  startMovement=millis();
  stepperSpeed = MIN_STEPPER_SPEED;

  int target = (int)  (((float)params.stepCm / 10.0f) * ((float)distance * (float)params.lineSteps / 100.0f));
#ifdef INVERT_DIRECTION
  target = target * -1;
#endif
  stepper1.moveTo(target);
  stepper2.moveTo(-target);
}

void turnLeft(short angle) {
  isMoving = true;
  startMovement=millis();
  stepperSpeed = MIN_STEPPER_SPEED;

  int angleStep = (int)((float)angle / 90.0 * (float)params.turnSteps);
  stepper1.moveTo(angleStep);
  stepper2.moveTo(angleStep);
}

void turnRight(short angle) {
  isMoving = true;
  startMovement=millis();
  stepperSpeed = MIN_STEPPER_SPEED;

  int angleStep = (int)((float)angle / 90.0 * (float)params.turnSteps);
  stepper1.moveTo(-angleStep);
  stepper2.moveTo(-angleStep);
}

void saveParams() {
  EEPROM.put(0, params);
}

void loadParams() {
  Params savedParams;
  EEPROM.get(0, savedParams);
  if (savedParams.stepCm > 0 && savedParams.stepCm < 500) {
    params.stepCm = savedParams.stepCm;
  } else {
    params.stepCm = 140;
  }
  if (savedParams.turnSteps > 0 && savedParams.turnSteps < 5000) {
    params.turnSteps = savedParams.turnSteps;
  } else {
    params.turnSteps=1250;
  }
  if (savedParams.lineSteps > 0 && savedParams.lineSteps < 500) {
    params.lineSteps = savedParams.lineSteps;
  } else {
    params.lineSteps = 140;
  }
}

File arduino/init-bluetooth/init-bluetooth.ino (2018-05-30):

  //**********************************************
// bluetooth HC06 Module configuraiton
// based on http://nicolasz68.blogspot.fr/2012/09/module-bluetooth-jy-mcu-v104-pour.html
//
//
//***********************************************/
#include <SoftwareSerial.h>
#include <Servo.h>

#define RxD 12
#define TxD 13
SoftwareSerial BTSerie(RxD,TxD); 

String deviceSuffix="OoRoBoT-";
String pin = "0000";
Servo penServo;

/*
1 Sets the baud rate to 1200
2 Sets the baud rate to 2400
3 Sets the baud rate to 4800
4 Sets the baud rate to 9600
5 Sets the baud rate to 19200
6 Sets the baud rate to 38400
7 Sets the baud rate to 57600
8 Sets the baud rate to 115200
9 Sets the baud rate to 230400
A Sets the baud rate to 460800
B Sets the baud rate to 921600
C Sets the baud rate to 1382400    
*/
String baud = "4";

static const char s[] = "ABCDEFGHIJKLMNOPQRSTUVWXYZ0123456789";
int i=0;
String deviceName;

void setup() 
{ 
  randomSeed(analogRead(A1));
  deviceName=deviceSuffix+s[random(strlen(s)-1)]+s[random(strlen(s)-1)]+s[random(strlen(s)-1)]+s[random(strlen(s)-1)];
  
  Serial.begin(9600);
  delay(500); 
  penServo.attach(3);
  penServo.write(0);
  delay(500);
  penServo.detach();
  // Bluetooth module init
  pinMode(RxD, INPUT); 
  pinMode(TxD, OUTPUT); 
  BTSerie.begin(9600); // Change it after previous baud configuration
} 
void loop() 
{ 
  char recvChar;
  if (i==0) {
    Serial.println("Set name to "+deviceName);
    BTSerie.print("AT+NAME"+deviceName);
    delay(1000);
  } else if (i==1) {
    Serial.println("Set PIN Code to "+pin);
    BTSerie.print("AT+PIN"+pin);    
    delay(1000);
  } else if (i==2) {
    Serial.println("Set baud to "+baud);
    BTSerie.print("AT+BAUD"+baud);
    delay(1000);
  } else if (i==3) {
    Serial.println("Pret pour d'autres commandes AT"); 
    i++;
  } else if (i==4) {
    if (Serial.available()) { 
      recvChar = Serial.read(); 
      BTSerie.write(recvChar); 
    }         
  }
          
  bool c=false;
  while (BTSerie.available()) {
    recvChar = BTSerie.read(); 
    Serial.print(recvChar);
    c=true;
  } 
  if (c) {
    if (i<4) {
      i++;
     }
    Serial.println("");
  }
} 

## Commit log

2018-05-30 nouvelle roue 3D
    [roue.stl, roues.fcstd]
2018-05-31 add missing chamber
    [roues.fcstd]
2018-05-31 add first test of des
    [theKube.dxf]
